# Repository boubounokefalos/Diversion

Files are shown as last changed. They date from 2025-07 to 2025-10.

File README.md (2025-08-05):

Diversion MK_I (ALPHA State)
================
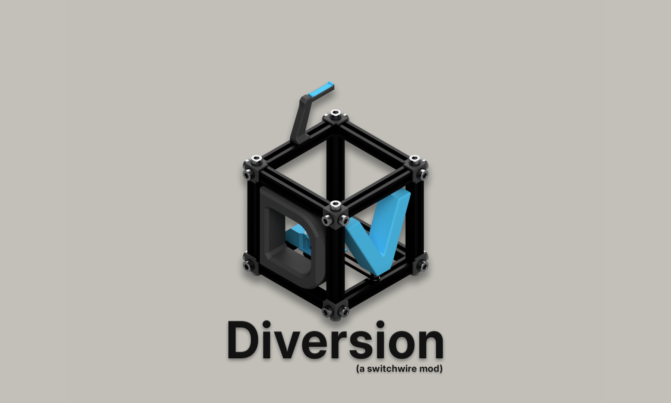
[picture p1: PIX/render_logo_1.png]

$\color{Red}{\textbf{My Disclaimer:}}$
--------------------------------
Diversion [dəˈvərZHən] is a [Switchwire](https://github.com/VoronDesign/Voron-Switchwire) <ins>mod</ins>. It is <ins>not</ins> an official Voron release, nor is it a scratch-built printer (it is based on the original Switchwire’s kinematics and construction). However, it is a project created with dedication and deep respect for the efforts of the entire community.

The Printer:
--------------
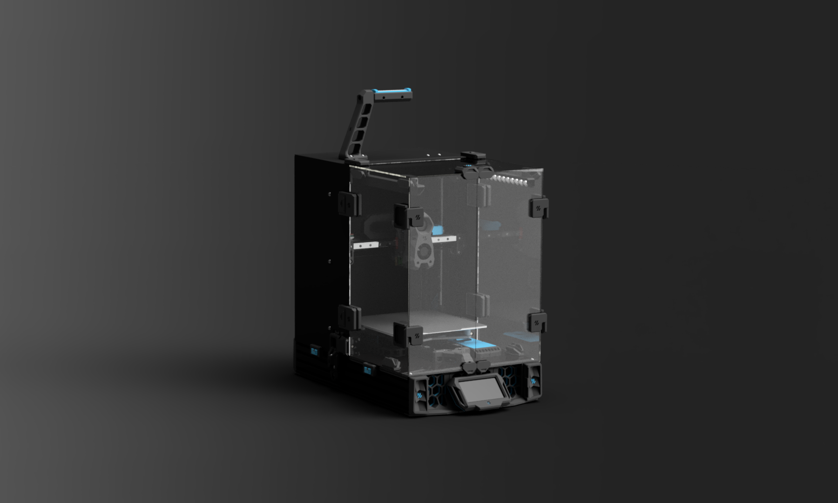
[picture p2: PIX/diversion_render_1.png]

The idea behind this project was to build a solid base using parts that are either easily accessible on the market or recycled from old printers that were lying around. I’ve always admired the subtle way the Voron Team designed their parts, but I wanted to exaggerate a bit while making a machine for my personal use.

The design is heavily influenced by improvements and modifications suggested by the community (credits for which can be found at the end of the page).

The basic hardware required for this build is similar to that of a typical Voron build. You will notice an excessive number of 6x3mm magnets (compared to a typical printer), which was necessary to achieve a clean and modular enclosure.

The Build:
--------------
The frame is similar to the Ender-to-SW conversion in the X and Z axes; however, the frame joints are blind joints this time. This helps with squaring (as long as the extrusion profiles have straight, unbotched ends) and improves rigidity.

Another distinctive feature is the use of 4080 C-beams for the lower part of the printer. Beyond structural integrity, they offer practical benefits such as deep channels for cable management on each side of the electronics bay and more mounting points for the XZ motor mounts.

The filter in this printer is a hybrid of nateb16’s [The Filter](https://github.com/nateb16/VoronUsers/tree/master/printer_mods/nateb16/THE_FILTER) and Nevermore's [Nevermore Micro V6](https://github.com/nevermore3d/Nevermore_Micro/tree/master/V6). The result is a compact component using an intact 5015 blower fan with a carbon cartridge that attaches to the plenum via magnets. The plenum neatly houses a female JST connector.

The enclosure is an attempt to improve on the original SW enclosure in the area that, in my opinion, had the greatest drawback: modularity. In Diversion’s enclosure, VHB tape is still used—but only to attach the magnetic brackets that hold it together. A large number of 6x3mm magnets were necessary to accomplish this, but now about 70% of the enclosure can be removed in under 30 seconds. The door hinges are 270°, easily detachable, and require no extra hardware—you just print them and assemble!

On the Y-axis, two parallel linear rails are used. They improve rigidity but require careful alignment (using the included brackets) to prevent binding during movement. An Ender 3 carriage drill jig is included, but the ideal option is to CNC the included Snowflake Y-carriage .step file.

BOM (WIP):
--------------
[Link](./docs/BoM.md)

Special Thanks to:
--------------------
+ Voron Team for providing a solid base to start from (The Original SW).
+ [Sooeeren](https://github.com/Sooeeren) for his valuable contribution with the BOM.
+ All of this loving 3D printing community on the Voron Discord servers.
+ Yenda and Strayr for the idea of the more robust x/z motors.
+ richardjm for his snap-latch-2020 mod, which is used with tiny modifications.

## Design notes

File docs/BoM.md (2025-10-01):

# BoM (Bill of Material) WIP

As always this list is intended as a helpful reference but it may not be entirely accurate or complete. Quantities can vary depending on specific build choices, mistakes during assembly, or future modifications, so it is always a good idea to order a few extra components where possible to avoid delays. If you come across any missing parts or notice anything that seems incorrect, please do not hesitate to let us know so we can update the list for everyone’s benefit. 

| Category | Component | QTY | Notes |
| --- | --- | :---: | --- |
| Fasteners | M3x5x4 Heatset Insert | 62 | These do not include the toolhead's inserts |
| | M6x16 BHCS | 16 | |
| | M5x40 SHCS | 6 | |
| | M5x30 BHCS | 4 | |
| | M5x25 BHCS | 1 | |
| | M5x20 BHCS | 3 | |
| | M5x16 BHCS | 7 | |
| | M5x10 BHCS | 63 | |
| | M5x8 BHCS | 20 | 8x of those are Optional -> Enclosure |
| | M4x25 FHCS | 4 | This size can vary, depending on the bed mounts |
| | M4x8 BHCS | 4 | |
| | M3x30 SHCS | 22 | |
| | M3x25 SHCS | 2 | |
| | M3x20 SHCS | 4 | |
| | M3x14 BHCS | 2 | |
| | M3x12 SHCS | 13 | |
| | M3x8 SHCS | 65 | |
| | M3x6 FHCS | 23 | |
| | M2x10 Self-Tapping | 6 | |
| | M5x1mm Spacer | 20 | |
| | M5 Nut | 3 | |
| | M3 Nut | 1 | |
| Motion | MGN12H 300mm | 5 | |
| | F695-2RS | 20 | |
| | GT2 20T 6mm | 3 | |
| | Belts | 4m | |
| | Door Pulling Device | 1 | 500gr is adequate. [AliExpress](https://www.aliexpress.com/item/1005007301954898.html?)
| Frame | 4080 C-Beams Extrusion 500mm | 2 | For people from the US you can source them [here](https://valuehobby.com/500mm-4080-c-beam-extrusion-2pcs.html)|
| | 2040 Extrusion 250mm | 2 | |
| | 2040 Extrusion 400mm | 2 | |
| | 2020 Extrusion 300mm | 2 | |
| | 2020 Extrusion 330mm | 1 | |
| | 2020 Extrusion 310mm | 1 | |
| Misc | 6mm x 3mm Round Neodymium Magnets | 98 | The excessive use of, preferably n52, magnets is mandatory for the modular design of the enclosure (you only need 90 if you are not using the BTT screen)|
| Electronics | 6020 Axial Fan | 1 | [GDStime](https://www.aliexpress.com/item/32899594270.html)  |
| | 50x50x15 Centrifugal Fan | 1 | |
| | Meanwell LRS-350-24 | 1 | |
| | BIGTREETECH SKR MINI E3 | 1 | |
| | Meanwell RS-25-5 | 1 | |
| | Raspberry Pi | 1 | |
| | Wago 221-413 | 3 | |
| | Mini12864 or BTT Pi43TFT | 1 | |
| | Power Inlet / Rocker Switch BV | 1 | [AliExpress](https://www.aliexpress.com/item/32706948395.html?)|
| | NEMA17 Motor 17HS15-1504S1	 | 2 | [Stepper Online](https://www.omc-stepperonline.com/nema-17-bipolar-45ncm-63-74oz-in-1-5a-42x42x39mm-4-wires-w-1m-cable-connector-17hs15-1504s1)|
| | KW10 Microswitch | 1 | |
| Buildplate | Ender 3/Pro Heatbed | 1 | Common 235x235 Ender heatbed. Can be either salvaged from an Ender or from various vendors |
| | Ender 3 Pro Pei Sheet + Magnet | 1 | |
| | Ender 3/Pro Carriage -> Option 1 | 1 | Custom Drilling Needed (drilling jig included in the STLs) |
| | Snowflake Custom Carriage -> Option 2 | 1 | Best and a bit pricier option. [JLCCNC](https://jlccnc.com/) is a nice source, use Aluminum 7075|
| | Silicon Spacers or Springs | 4 | Both of them work, best option is the silicon spacers |
| | Curled Nuts | 4 | [AliExpress](https://aliexpress.com/item/1005005147484464.html)|
| Other | Switchwire Cable Chain Kit | 1 | |
| | Activated Carbon | 1 | |
| | PTFE Tube | 1 | |
| Panels | Deck Panel Left | 1 | |
| | Deck Panel Right | 1 | |
| | Deck Panel Bottom | 1 | |
| | Deck Panel Bottom-Mid | 1 | |
| | Enclosure Panels | 9 | Optional |
| Wiring | 10x11 Cable Chain - Openable (1m) | 2 | |
| | 16AWG Silicone Cable (10ft total) | 2 | |
| | 20AWG Silicone Cable (10ft total) | 1 | |
| | 24AWG Silicone Cable (100ft total) | 1 | |
| | Fork Spade Terminal | 15 | |
| | Insulated Crimp Receptical | 10 | |
| | JST-XH Connector Plug 2 Position | 4 | |
| | JST-XH Connector Plug 3 Position | 1 | |
| | JST-XH Connector Plug 4 Position | 4 | |
| | JST-XH Female Pin | 40 | |
| | MicroFit Connector Plug 2 Position (43640-0201) | 6 | |
| | MicroFit Connector Plug 3 Position (43640-0301) | 1 | |
| | MicroFit Connector Plug 4 Position (43640-0401) | 1 | |
| | MicroFit Connector Receptacle 2 Position (43645-0200) | 6 | |
| | MicroFit Connector Receptacle 3 Position (43645-0300) | 1 | |
| | MicroFit Connector Receptacle 4 Position (43645-0400) | 1 | |
| | MicroFit3 Female Pin (43030-0007) | 40 | |
| | MicroFit3 Male Pin (43031-0007) | 40 | |
| | Nylon Cable Ties 4" | 100 | |
| Stealthburner | Mounting screws (M2.5 / M3) | 2-4 | |
| | M3x8 SHCS | 4 | |
| | M3x6 FHCS | 3 | |
| | M3x6 BHCS | 1 | |
| | M3x50 SHCS | 2 | |
| | M3x30 SHCS | 1 | |
| | M3x25 SHCS | 6 | |
| | M3x20 SHCS | 1 | |
| | M3x16 SHCS | 4 | |
| | M3x12 SHCS | 2 | |
| | M3 Washer | 1 | |
| | M3 Threaded Insert | 17 | |
| | Bondtech BMG Extruder Kit | 1 | |
| | NeoPixel RGBW Mini Button PCB | 3 | |
| | NEMA14 36mm pancake Motor w/ 10 tooth gear | 1 | |
| | 50x50x15 Centrifugal Fan | 1 | |
| | 40x40x10 Axial Fan | 1 | |
| | M3x12 SHCS (ADXL345 Sensor) | 2 (optional) | |
| | M3 Threaded Insert (ADXL345 Sensor) | 2 (optional) | |
| | M2x10 Self-Tapping (ADXL345 Sensor) | 2 (optional) | |
| | Harness for ADXL Sensor | 1 (optional) | |
| | ADXL345 Sensor Module | 1 (optional) | |
| | Toolhead PCB (SB Compatible) | 1 (optional) | |
| | M3x8 SHCS (Toolhead PCB) | 2 (optional) | |
| | M3 Threaded Insert (Toolhead PCB) | 2 (optional) | |
| | Harness for Toolhead PCB | 1 (optional) | |

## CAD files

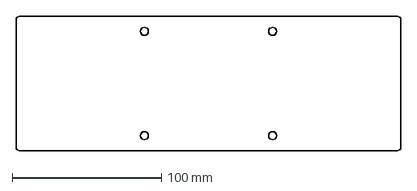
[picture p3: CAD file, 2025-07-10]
DXF/Decks/deck_under_mid.dxf
258.0 x 90.0 mm

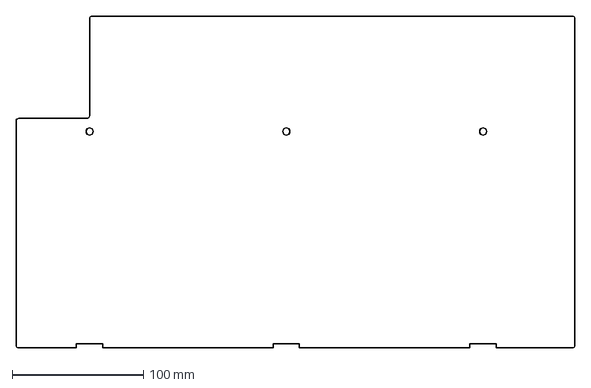
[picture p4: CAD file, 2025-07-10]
DXF/Enclosure Panels/black_rear_sidepanel_2.dxf
426.0 x 253.0 mm

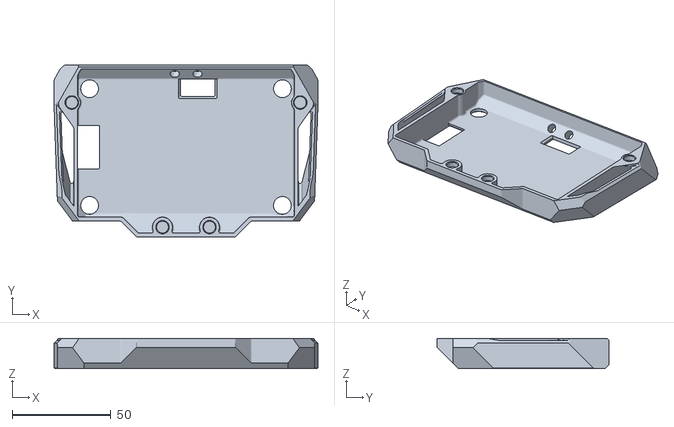
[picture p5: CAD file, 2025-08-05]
STLS/Electronics/lcd_case_rear_bttpi43tft.stl
133.5 x 87.0 x 15.4

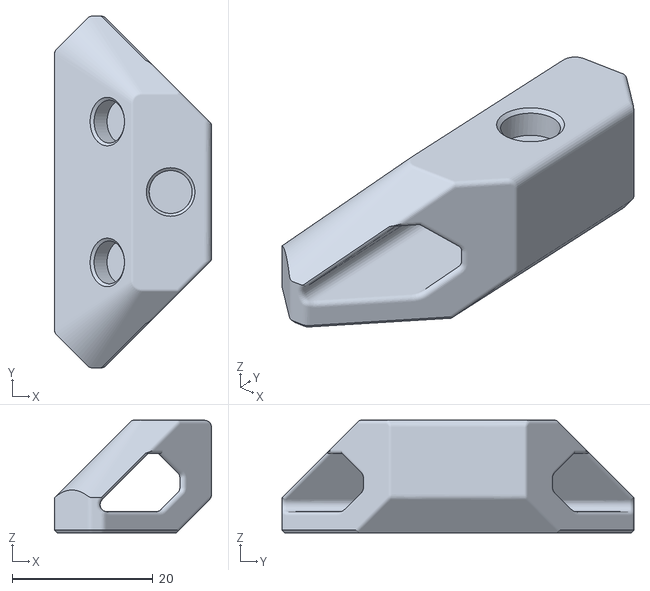
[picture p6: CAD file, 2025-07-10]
STLS/Enclosure/side_brackets_lightbar_magnet_x4.stl
22.3 x 50.0 x 16.0

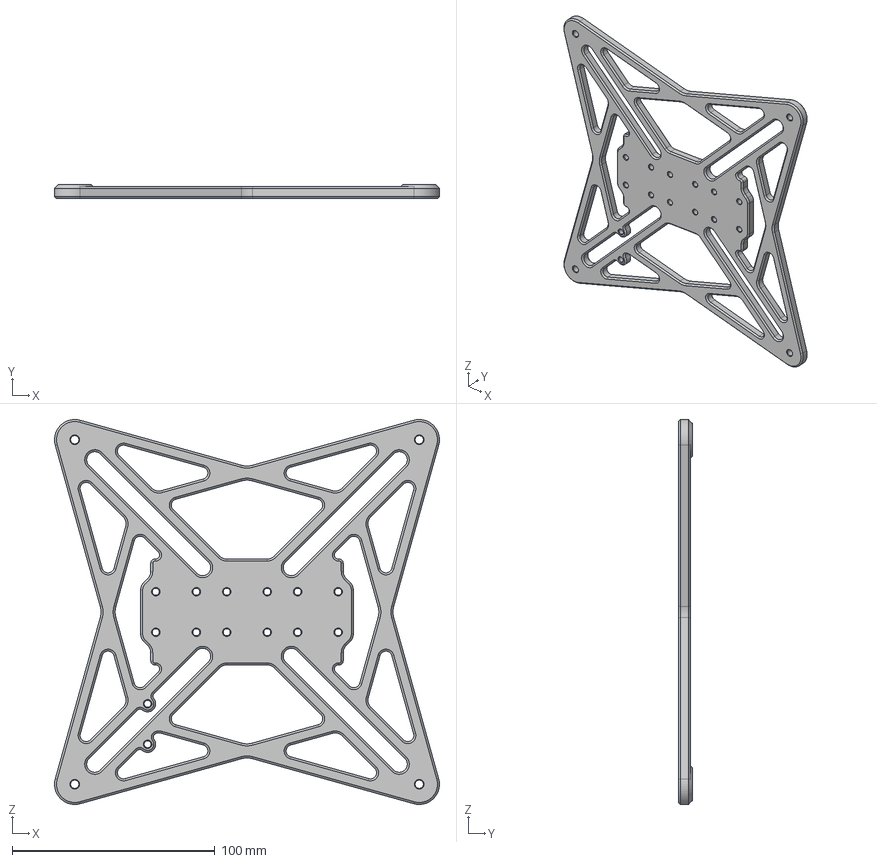
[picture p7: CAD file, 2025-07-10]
STLS/Extras/Snowflake Y Carriage.step
190.0 x 7.00 x 190.0 mm

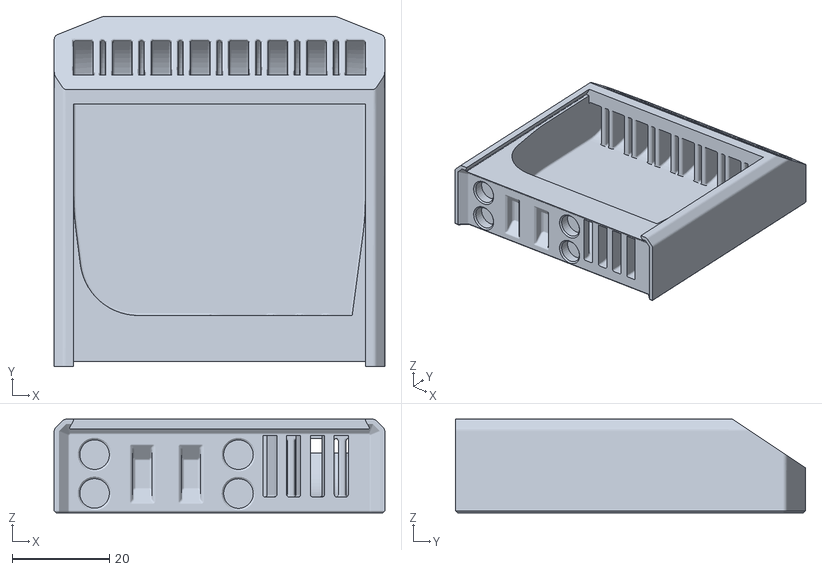
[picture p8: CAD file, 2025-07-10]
STLS/Filter/cartridge.stl
68.0 x 72.0 x 19.2

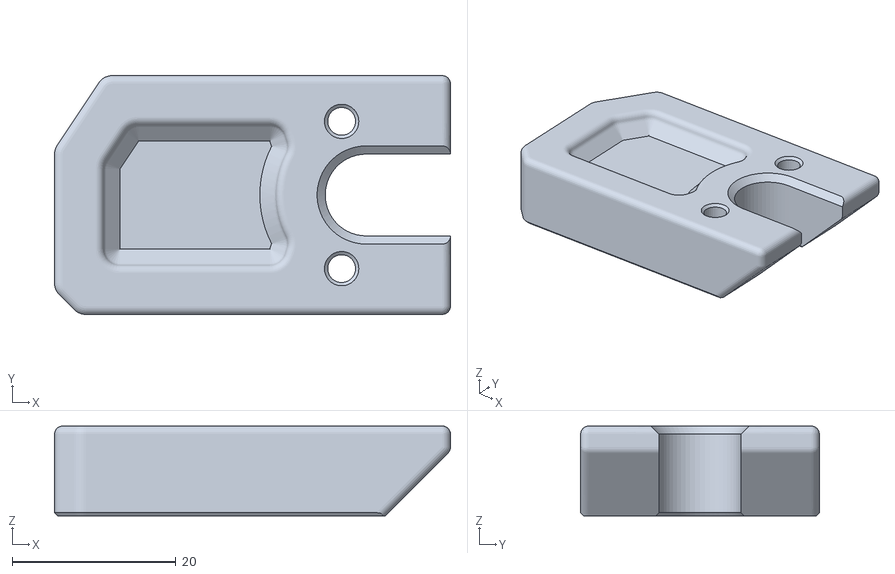
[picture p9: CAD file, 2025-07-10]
STLS/Gantry/XZ Axis/z_chain_arm_right_generic.stl
48.4 x 29.2 x 11.0

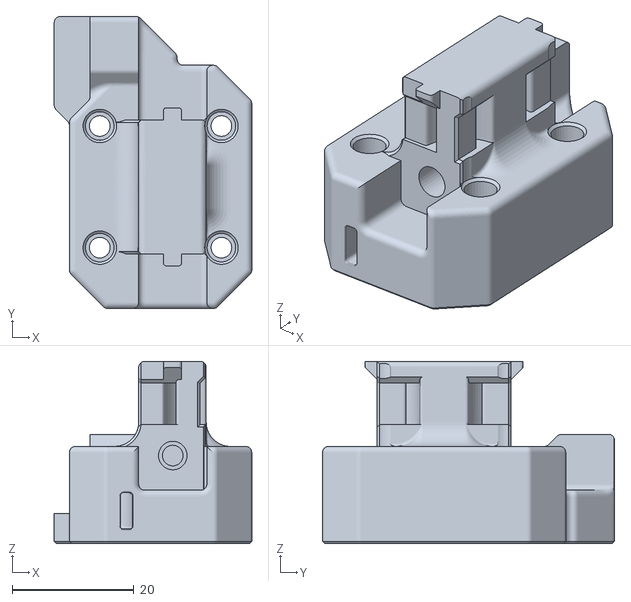
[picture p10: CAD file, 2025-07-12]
STLS/Gantry/Y axis/y_belt_anchor.stl
32.5 x 48.0 x 30.0

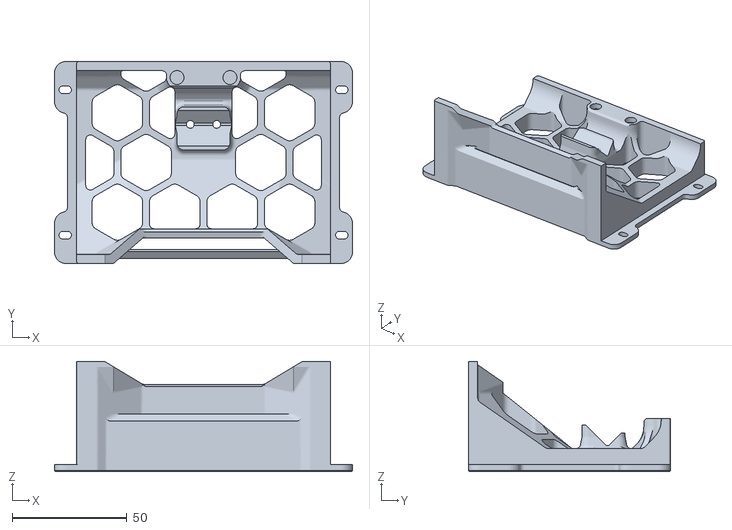
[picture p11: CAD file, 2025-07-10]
STLS/Grills/gril_mid_front.stl
129.8 x 88.0 x 47.9

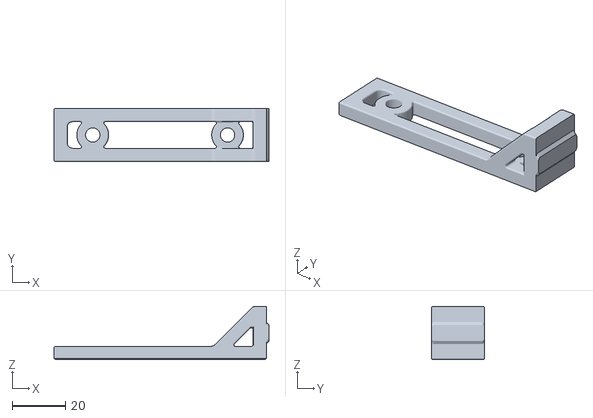
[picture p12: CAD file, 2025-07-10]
STLS/Jigs/y_align_side_x2.stl
81.0 x 20.0 x 20.0

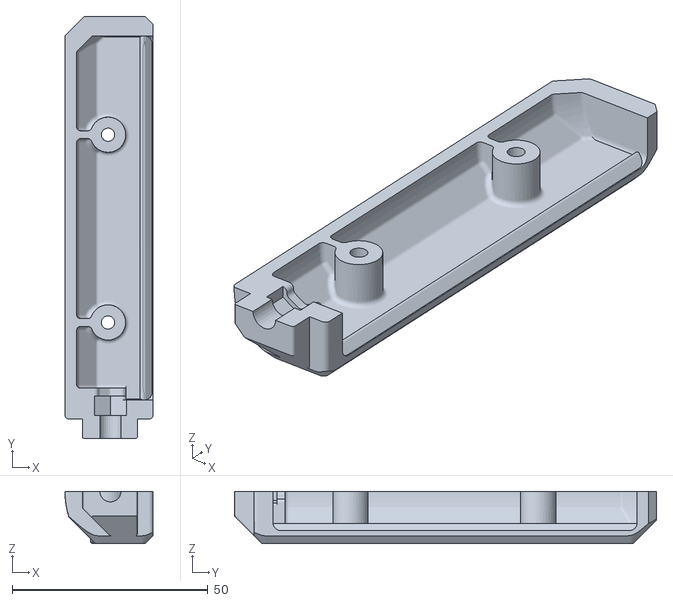
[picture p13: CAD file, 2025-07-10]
STLS/Misc/spool_holder_a.stl
22.6 x 107.9 x 13.3

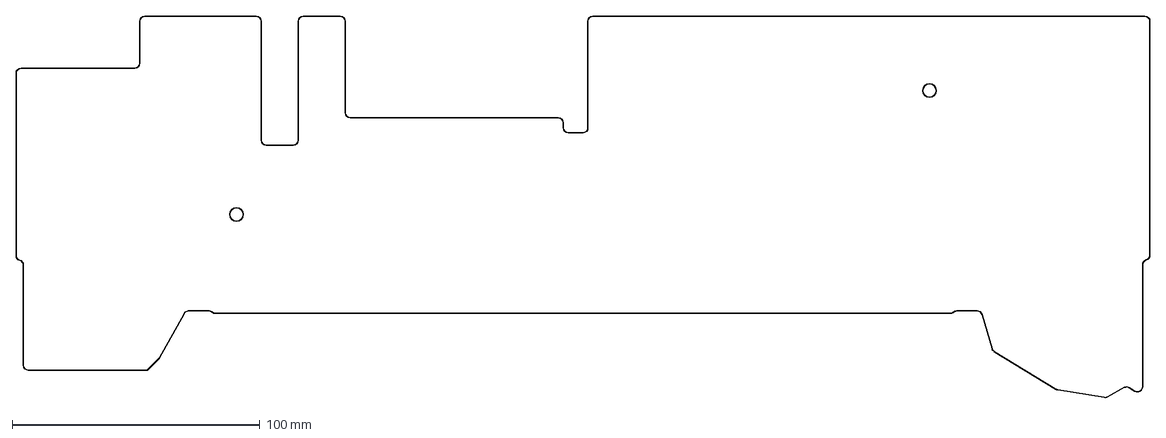
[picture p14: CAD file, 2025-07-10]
DXF/Decks/deck_right.dxf
458.0 x 154.0 mm

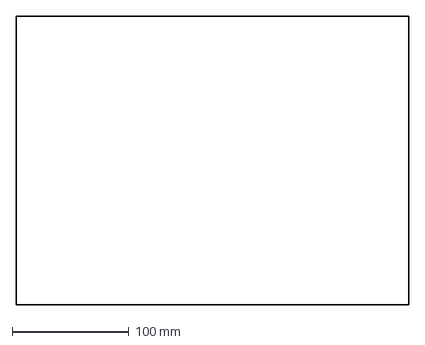
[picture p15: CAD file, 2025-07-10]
DXF/Enclosure Panels/clear_toppanel.dxf
336.0 x 247.0 mm

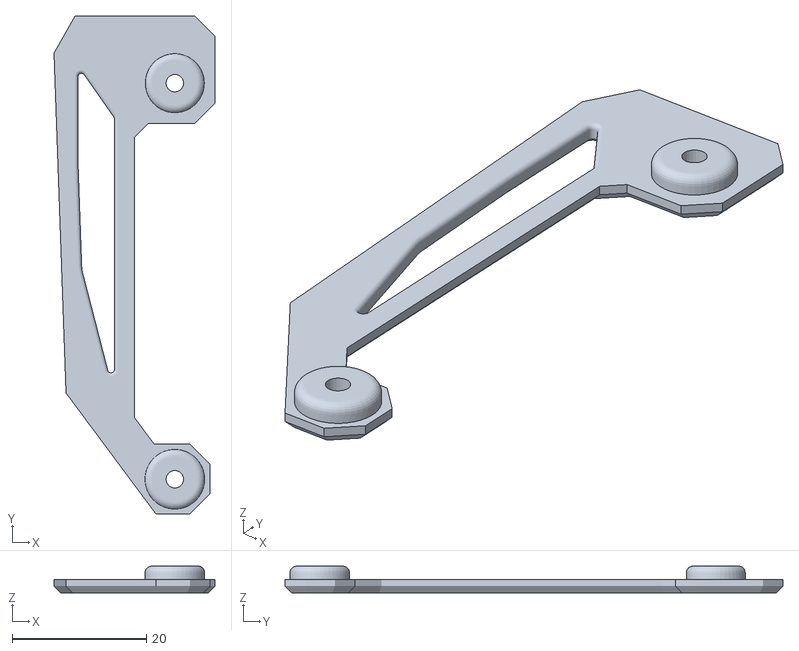
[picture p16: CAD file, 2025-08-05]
STLS/Electronics/[a]_accent grill_right_bttpi43tft.stl
24.0 x 74.2 x 4.00

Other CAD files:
STLS/Enclosure/side_bracket_deck_x2.stl
STLS/Extras/nitehawk_adapter_mount_cover.stl
STLS/Filter/[a]_fan_clamp.stl
STLS/Gantry/XZ Axis/upper_idler_support_a_right.stl
DXF/Decks/deck_left.dxf
DXF/Decks/deck_under.dxf
DXF/Enclosure Panels/black_rearpanel.dxf
DXF/Enclosure Panels/black_toppanel.dxf
DXF/Enclosure Panels/clear_door1.dxf
DXF/Enclosure Panels/clear_door2.dxf
DXF/Enclosure Panels/clear_sidepanel_1.dxf
DXF/Enclosure Panels/clear_sidepanel_2.dxf
STLS/Electronics/6020_fan_mount.stl
STLS/Electronics/PS_2040_mount_a.stl
STLS/Electronics/PS_2040_mount_b.stl
STLS/Electronics/PS_4080_side_mount_a.stl
STLS/Electronics/PS_4080_side_mount_b.stl
STLS/Electronics/RS_4080_mount_a.stl
STLS/Electronics/RS_4080_mount_b.stl
STLS/Electronics/Rpi_2040_mount_a.stl
STLS/Electronics/Rpi_2040_mount_b.stl
STLS/Electronics/[a]_accent grill_left_bttpi43tft.stl
STLS/Electronics/[a]_logo_bg_bttpi43tft.stl
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

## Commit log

2025-07-10 Initial Commit
    That's how it all started...
    [6020_fan_mount.stl, PS_2040_mount_a.stl, PS_2040_mount_b.stl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]
2025-07-10 Fix typo on file name
    [lcd_case_front_mini12864.stl]
2025-07-10 Add link to the Official Voron SwitchWire.
2025-07-10 add BOM
2025-07-10 update BOM
2025-07-12 Updated y_anchor
    slight adjustment of y_anchor to improve clearance of the bed when reaching the endstop.
    [y_belt_anchor.stl]
2025-07-22 Include access holes to the frame.
    Updated CAD to include access holes to the frame (for the blind joints).
2025-08-05 Added BTT Pi43TFT support
    Added BTT Pi43TFT support and updated all files accordingly
    [[a]_accent grill_left_bttpi43tft.stl, [a]_accent grill_right_bttpi43tft.stl, [a]_logo_bg_bttpi43tft.stl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]
2025-10-01 Update BoM.md
    Added US source for the C-Beams
